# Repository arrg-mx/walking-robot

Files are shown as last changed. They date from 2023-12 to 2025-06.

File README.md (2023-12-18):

# ARRG: Curso ROS2 Humble, 2024-I - Walking Robot

## Contenido

- [Desarrollo](#desarrollo)
- [Equipo](#equipo)
- [Referencias](#referencias)

## Desarrollo

- [X ] Documentación y justificación de la configuración del robot.
- [X ] Planteamiento del modelo cinemático directo de la postura y planteamiento del modelo cinemático inverso de la postura.
- [ ] Diseño e implementación de un modelo virtual del caminante.
	- [X ] Modelo de una pierna del robot.
	- [ ] Modelo del robot completo.
- [ ] Realización de las pruebas dentro del modelo virtual y reporte de resultados.
- [ X] Construcción de un modelo físico del robot.
	- [ X] Construcción de una pierna del robot.
	- [ ] Construcción de la estructura del robot.
- [ ] Implementación de los resultados en el prototipo físico.
	- [ ] Prototipo de una pierna.
	- [ ] Prototipo del robot completo
- [ ] Reporte de resultados finales.
- [ ] Conclusiones y Discusión

## Equipo

**Integrantes del proyecto:**

| Nombre | Observaciones |
| :---| :--- |
| Hernández Romero Naomi Estefanía | **responsable** |
| Vargas Gutiérrez Kevin | |
| Hernández Hernández Danae Montserrat | |
| Martínez Merino Luis Eduardo | |

## Referencias

### ¿Dónde empezar?

**Artículos**

1. **Control of a Hexapod Robot Considering Terrain Interaction** [Arxiv Cornell University - article](https://arxiv.org/abs/2112.10206)
	> M. Zangrandi, S. Arrigoni, and F. Braghin, Control of a Hexapod Robot Considering Terrain Interaction. 2021. 
	> 
	> doi: 10.48550/arXiv.2112.10206
1. *Real-Time Stabilisation for Hexapod Robots* **DOI:** <https://doi.org/10.1007/978-3-319-23778-7_48>
	> M. Hörger, N. Kottege, T. Bandyopadhyay, A. Elfes, and P. Moghadam, “Real-Time Stabilisation for Hexapod Robots,” in Experimental Robotics: 
	> The 14th International Symposium on Experimental Robotics, M. A. Hsieh, O. Khatib, and V. Kumar, Eds. Cham: Springer International Publishing, 2016, pp. 729–744. 
	> 
	> doi: 10.1007/978-3-319-23778-7_48. 
1. **Kinematic and Dynamic Modeling of the PhantomX AX Metal Hexapod Mark III Robot using Quaternions**	[IEEE article](https://ieeexplore.ieee.org/abstract/document/9624596)
	> A. J. P. A. Chávez and J. H. A. Alcántara, "Kinematic and Dynamic Modeling of the PhantomX AX Metal Hexapod 
	> Mark III Robot using Quaternions," 2021 International Conference on Control, Automation and Information Sciences (ICCAIS), Xi'an, China, 2021, pp. 595-601, 
	>
	> doi: 10.1109/ICCAIS52680.2021.9624596.
1. **Dynamic Modeling and Control of the Hexapod Robot Using Matlab SimMechanics** [ResearchGate article](https://www.researchgate.net/publication/330405549_Dynamic_Modeling_and_Control_of_the_Hexapod_Robot_Using_Matlab_SimMechanics)
	> Beaber, Sameh & Zaghloul, Abdelrahman & Kamel, Mohamed & Hussein, Wessam. (2018). Dynamic Modeling and Control of the Hexapod Robot Using Matlab SimMechanics. 
	> V04AT06A036. 10.1115/IMECE2018-88226. 
	>
	> DOI:10.1115/IMECE2018-88226
1. **Locomotion Control of PhantomX Hexapod Robot with Touch-Pressure Sensor and RoboComp**	[ResearchGate article](https://ieeexplore.ieee.org/abstract/document/9247874).
	> J. E. C. Fuertes, J. J. M. Arciniegas, P. B. G. de Castro and O. A. V. Albán, "Locomotion Control of PhantomX Hexapod Robot with Touch-Pressure Sensor and RoboComp," 
	> 2020 IEEE Colombian Conference on Applications of Computational Intelligence (IEEE ColCACI 2020), Cali, Colombia, 2020, pp. 1-6, 
	> 
	> doi: 10.1109/ColCACI50549.2020.9247874.
1. **Dynamic modeling and real-time evaluation of reaction forces and torques of hexapod robot** [ResearchGate article](https://www.researchgate.net/publication/350820943_Dynamic_modeling_and_real-time_evaluation_of_reaction_forces_and_torques_of_hexapod_robot)
	> S. Beaber, A. Zaghloul, M. Kamel, and W. Hussein, “Dynamic modeling and real-time evaluation of reaction forces and torques of hexapod robot,” Apr. 2021, p. 30. 
	> 
	> doi: 10.1117/12.2596113. 
1. **Design, Construction, and Rough-Terrain Locomotion Control of Novel Hexapod Walking Robot With Four Degrees of Freedom Per Leg** [IEEE article](https://ieeexplore.ieee.org/abstract/document/9330519)
	> P. Čížek, M. Zoula and J. Faigl, "Design, Construction, and Rough-Terrain Locomotion Control of Novel Hexapod Walking Robot With Four Degrees of Freedom Per Leg," 
	> in IEEE Access, vol. 9, pp. 17866-17881, 2021, 
	>
	> doi: 10.1109/ACCESS.2021.3053492.

**Blogs**

1. *Love, Death, and Robot simulators* [medium post](https://medium.datadriveninvestor.com/love-death-and-robot-simulators-9ad7c62d46ae). 
	- **Posted by:** [Mithi](https://medium.com/@mithi?source=post_page-----9ad7c62d46ae--------------------------------)
	- **Published:** March 30, 2020
	- **Posted in:** [DataDrivenInvestor](https://medium.datadriveninvestor.com/?source=post_page-----9ad7c62d46ae--------------------------------)
	- **Source Code:**
 		- **Mithi's Bare-Minimum Hexapod Robot Simulator 2** [Github repository](https://github.com/mithi/hexapod)
		- **Hexapod Kinematics Library** [Github repository](https://github.com/mithi/hexapod-kinematics-library). By [**Mithi Sevilla´s** Github Profile](https://github.com/mithi). Code you can use to solve forward/inverse kinematics and generate walk sequences of hexapod robots. 
 	- **Live demo:** <https://hexapod.netlify.app/>
  	- **Hexapod Robot Inverse kinematics Visualizer (with Javascript and React)** [YT video](https://www.youtube.com/watch?v=FxjfTUj2Dk0)
	- **Tags:** [Robotics](https://medium.com/tag/robotics?source=post_page-----9ad7c62d46ae---------------robotics-----------------), 
	[Artificial Intelligence](https://medium.com/tag/artificial-intelligence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), 
	[Open Source](https://medium.com/tag/open-source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), 
	[Electronics](https://medium.com/tag/electronics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), 
	[Coding](https://medium.com/tag/coding?source=post_page-----9ad7c62d46ae---------------coding-----------------)

**Legacy/Opensource Projects, Applications and, Libraries**

1. **Interbotics ROS Crawlers** [github repository](https://github.com/Interbotix/interbotix_ros_crawlers). ***ROS2 Humble*** *Compatible*
	- This repo contains custom ROS packages to control the various types of crawlers sold at [Interbotix](https://www.trossenrobotics.com/). 
	- These ROS packages build upon the ROS driver nodes found in the [interbotix_ros_core](https://github.com/Interbotix/interbotix_ros_core) *repository*. 
	- Support-level software can be found in the [interbotix_ros_toolboxes](https://github.com/Interbotix/interbotix_ros_toolboxes) *repository*.
1. **PhantomX Hexapod Mark II**
	- Google search [results](https://www.google.com/search?client=firefox-b-d&q=PhantomX+Hexapod+Mark+II)
	- **PhantomX AX Metal Hexapod MK-III Kit** [Trossen Robotics #Item](https://www.trossenrobotics.com/phantomx-ax-hexapod.aspx)
	- **PhantomX AX Metal Hexapod Mark III** [YT video](https://www.youtube.com/watch?v=8v16kpBj9JQ). [Trossen Robotics - YT channel](https://www.youtube.com/@InterbotixTrossenRobotics)
	- **PhantomX Hexapod Mark II** [GrabCad model](https://grabcad.com/library/phantomx-hexapod-mark-ii-1)
	- **HumaRobotics**
		- **phantomx_description** [github repository](https://github.com/HumaRobotics/phantomx_description)
		- **phantomx_control** [github repository](https://github.com/HumaRobotics/phantomx_control)
		- **phantomx_gazebo** [github repository](https://github.com/HumaRobotics/phantomx_gazebo)
		- **geomagic_touch** [github repository](https://github.com/HumaRobotics/geomagic_touch)
	- **PhantomX Hexapod Examples Various demos for the PhantomX Hexapod** [github repository](https://github.com/Interbotix/PhantomXHexapodExamples)
1. **hexapod-robot** [github repository](https://github.com/ibarbech/hexapod-robot)
1. **ROS Hexapod Stack** [github repository](https://github.com/KevinOchs/hexapod_ros/tree/master)
1. **Syropod High-level Controller** [Github repository](https://github.com/csiro-robotics/syropod_highlevel_controller)
	- **OpenSHC: A Versatile Multilegged Robot Controller** [YT video](https://www.youtube.com/watch?v=-E7-2UMP5XU)
	- **Note:** The codebase is largely copied from [Mithi's Bare Minimum Hexapod Robot Simulator 2](https://github.com/mithi/hexapod).
1. **Hexi** *(project)* [about](https://hexyrobot.wordpress.com/)
	- [Github repository](https://github.com/mithi/hexy)
1. **TOPS** *(Traverser of Planar Surfaces) or SPOT backward is a 12DOF quadrupedal robot.*
	- [project page](https://www.aaedmusa.com/projects/tops)
 	- [Hackaday's project page](https://hackaday.io/project/192122-tops)
  	- CAD, Code, BOM, etc... [Github repository](https://github.com/aaedmusa/TOPS)
   	- *I Built a Robotic Actuator.......Lets Test it!* [Part 0 - YT video](https://www.youtube.com/watch?v=gxXatMr0LX4)
   	- *Robot Dog Part 1: Leg Day* [Part 1 - YT video](https://www.youtube.com/watch?v=cqpYpj8EaDY)
   	- *Robot Dog Part 2: Leg Redesign* [Part 2 - YT video](https://www.youtube.com/watch?v=bdJuIe2igCI)
   	- *I Built a Robot Dog and Made it Dance* [Part 3 - YT video](https://www.youtube.com/watch?v=VhUvoV5XyRg)
1. **openDog V3: How I made it Walk** [YT video](https://www.youtube.com/watch?v=eKZIJwJBjEs). By [James Bruton](https://www.youtube.com/@jamesbruton)
	- *CAD and code* [openDogV3- Github repository](https://github.com/XRobots/openDogV3) 

---

**Nota:** Usar la siguiente [plantilla](https://github.com/arrg-mx/fmtos-docs/blob/main/fmto-reporte-curso.md) para su reporte así como la [plantilla del repositorio](https://github.com/mrg-mex/mrg-plantilla-repositorio) como una guía para organizar sus archivos y referencia del formato Markdown para diferentes elementos que necesiten integrar en su reporte.

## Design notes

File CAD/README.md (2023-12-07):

# Carpeta para archivos de CAD del proyecto
Los archivos de todo el CAD se encuentran en el archivo comprimido Modelos.rar

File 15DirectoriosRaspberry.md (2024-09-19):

# Creacion del entorno de trabajo 

> mkdir ROS2_dev

>cd ROS2_dev

>mkdir hexapod_ws

>cd hexapod_ws

>mkdir src

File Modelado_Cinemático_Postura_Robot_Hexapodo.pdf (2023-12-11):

## UNIVERSIDAD NACIONAL AUTÓNOMA DE MÉXICO

## Facultad de Ingeniería Ingeniería Mecatrónica

# ROBÓTICA

## Proyecto Final - Robot Hexapodo

## Profesor: Erik Peña Medina

## Integrantes: - Capulín Ornelas Arturo Misael - Hernández Hernández Danae Monserrat - Hernández Romero Naomi Estefanía - Jiménez Díaz César David - Vargas Gutiérrez Kevin

## Ciudad de México, 08 de diciembre de 2023

## Modelado de la pata del hexapodo en el espacio

## Método de transformaciones homógeneas

El método de transformaciones homógeneas consiste en describir las relaciones de posición y orientación entre cada uno de los elementos que conforman la estructura mecánica de un robot, para describir dichas relaciones se establece una matriz la cual contiene las relaciones entre las translaciones sobre cada uno de los ejes y las rotaciones sobre cada uno de los ejes. En la Figura (3), se presentan las relaciones que describen las
translaciones para describir a posición del orienten de un sistema | con respecto el origende un sistema
anterior | .

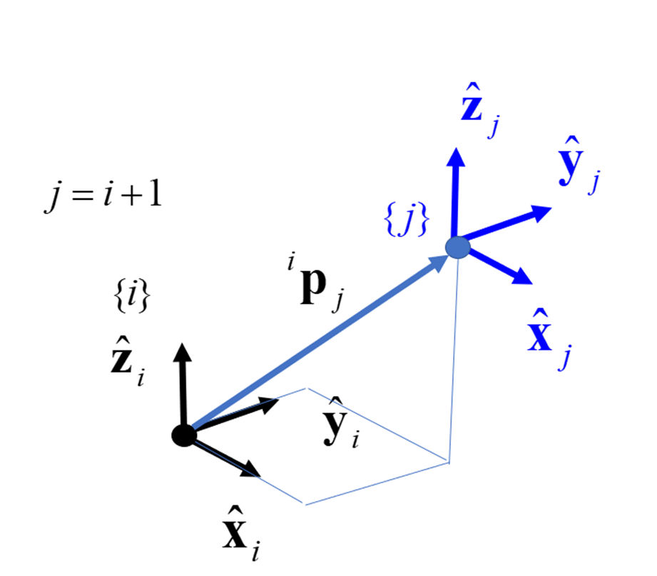
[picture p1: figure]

Figura 3. Planteamiento de la descripción de la posción del sistema | con respecto a un sistema | .
La posición del sistema | con respecto al sistema | , se compone de tres transformaciones que describen
las translaciones sobre cada uno de los ejes coordenadas del sistema | .

Las posición del sistema | con respecto al sistema | se describe mediante la combinación de las
transformaciones anteriores, conformando la transformación | :

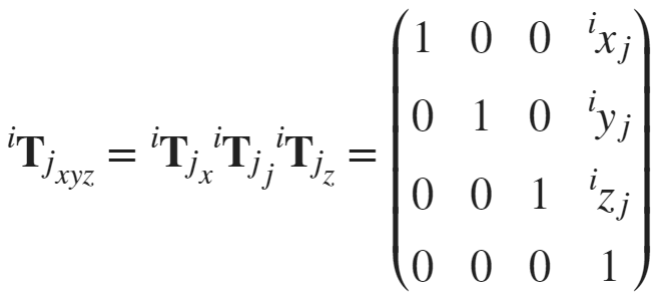
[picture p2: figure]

La orientación del sistema de referencia se establece mediante la combinación de matrices que contiene las relaciones de orientación con respecto a cada uno de los ejes del sistema .

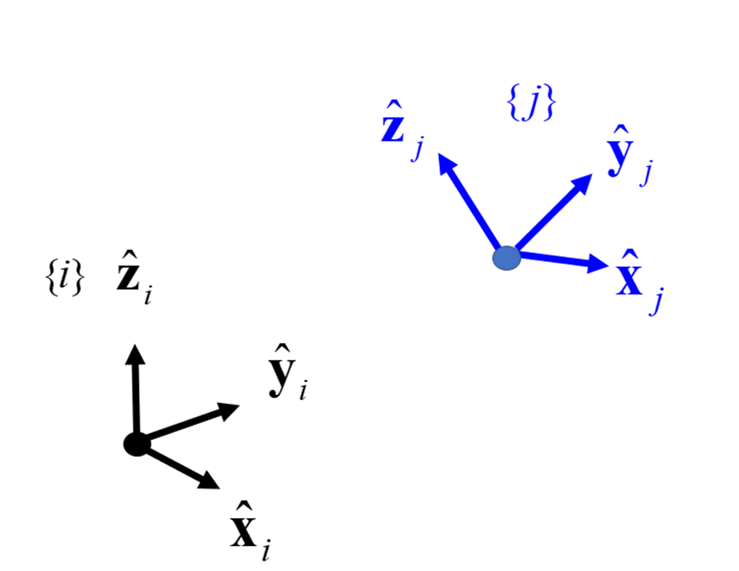
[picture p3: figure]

Figura 4. Planteamiento de la descripción de la orientación del sistema | con respecto a un sistema | .
Las relaciones que describen la orientación al eje | (Figura 5) se establece mediante la transformación

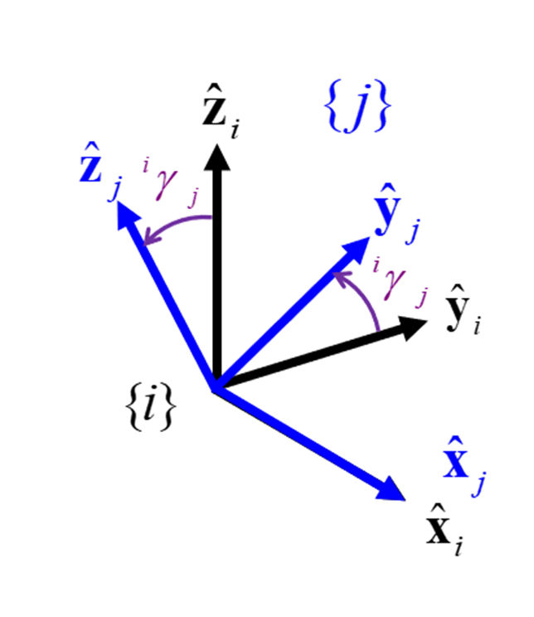
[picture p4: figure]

Figura 5. Planteamiento de la descripción de la orientación del sistema | con respecto a un sistema | con
respecto al eje .

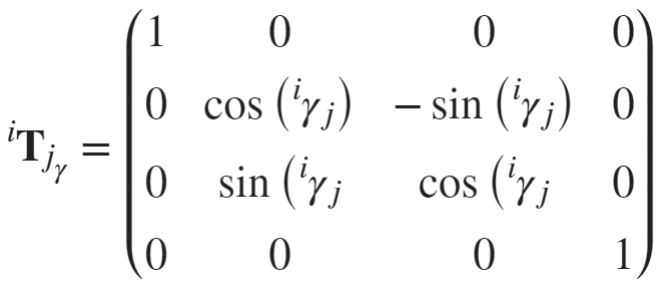
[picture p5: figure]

Las relaciones que describen la orientación al eje | (Figura 6) se establece mediante la transformación | .

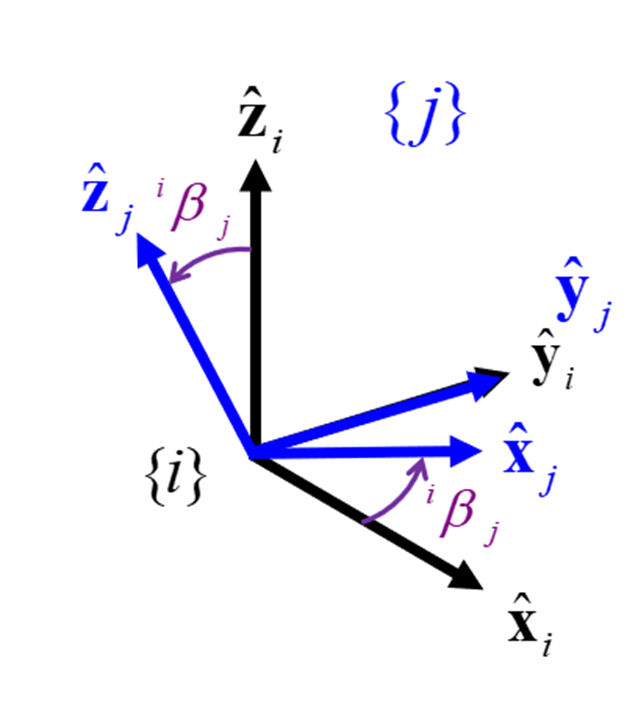
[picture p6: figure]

Figura 6. Planteamiento de la descripción de la orientación del sistema | con respecto a un sistema | con
respecto al eje .

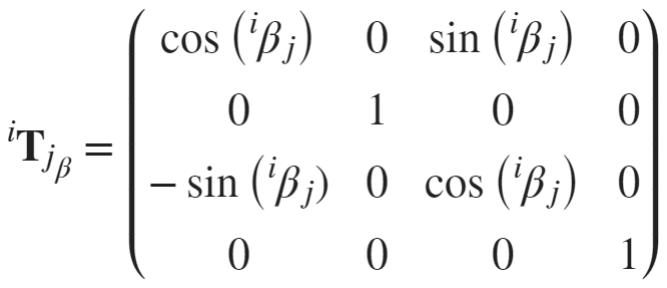
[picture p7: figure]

Las relaciones que describen la orientación al eje | (Figura 7) se establece mediante la transformación | .

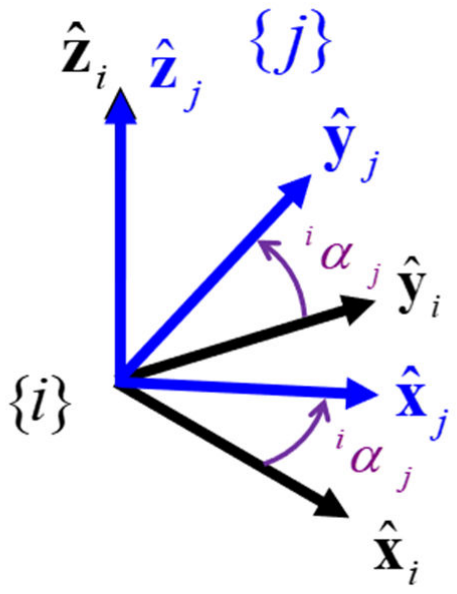
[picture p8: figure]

Figura 7. Planteamiento de la descripción de la orientación del sistema | con respecto a un sistema | con
respecto al eje .

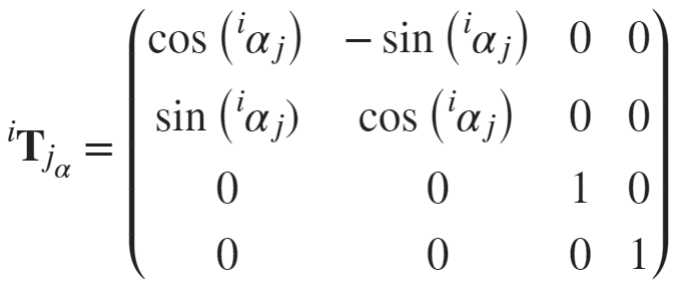
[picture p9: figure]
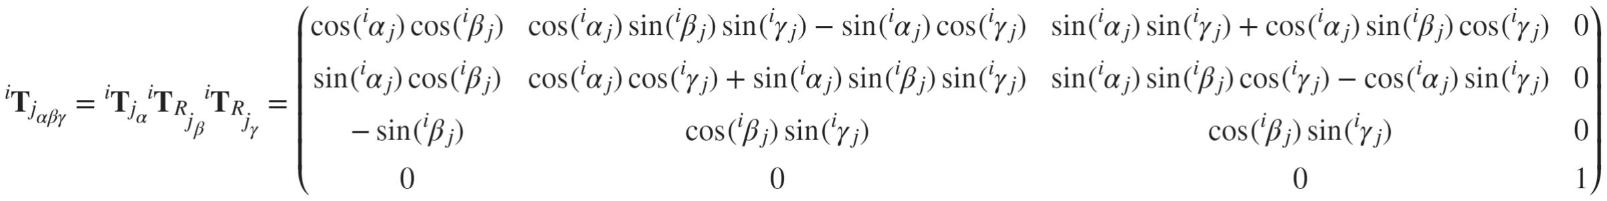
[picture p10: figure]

Para conformar la transformación que describre las relaciones de posición y orientación entre dos sistemas de referencias se establece la transformación :

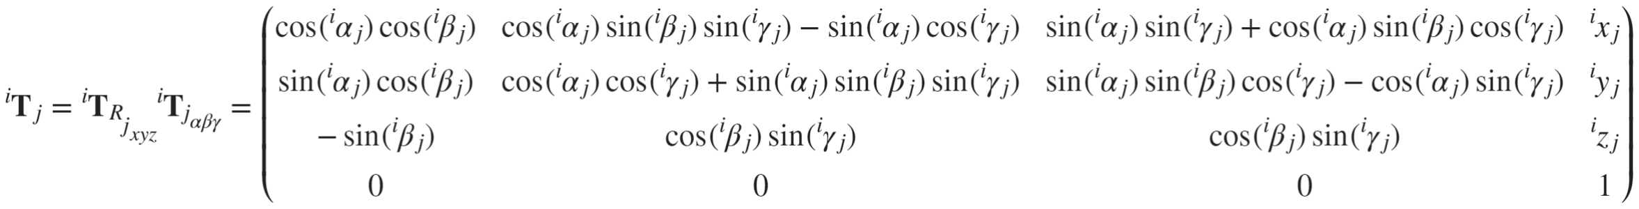
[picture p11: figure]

Para mostrar como se emplean las transformaciones homógeneas se plantea el ejemplo en el cual se obtiene el modelo matemático de la postura de un robot PUMA 560.

Planteamiento del modelo de la postura por el método de transformaciones homógenas

Para establecer el modelo cinemático de la postura de la pata del hexapodo es necesario definir una postura de "Home" en la cual el robot comezará a operar de forma segura, además de la cual se establecerán las ecuaciones que describan al robot. Ya definida la postura de "Home", se debe de seguir los siguientes pasos para establecer el modelo matemático que describa la postura de un robot en función de sus variables de postura:

1. Determinar el sistema inercial.
2. Encontrar los ejes de acción de los actuadores.
3. Sobre los ejes de actuación establecer los sistema de referencias que rescriban las relaciones de movimiento entre una junta y un eslabón.
4. Establecer los parámetros y las variables de posición y orientación entre los sistemas de referencia de cada eslabón hasta llegar el sistema {P}.
5. Colocar los parámetros en la tabla de configuración y de variables.
6. Calcular la ecuación del modelo cinemático de la postura.

1.Determinación del sistema inercial

Para establecer un sistema el modelo un robot es necesario establecer un sistema de referencia por el cual se estableceran las relaciones posición y orientación del efector final de un robot, para este caso se establecerá
un sistema inercial el cual permanecerá fijo y se establecerá como el sistema | y un sistema de referencia
relativo | asociado al EF del robot.

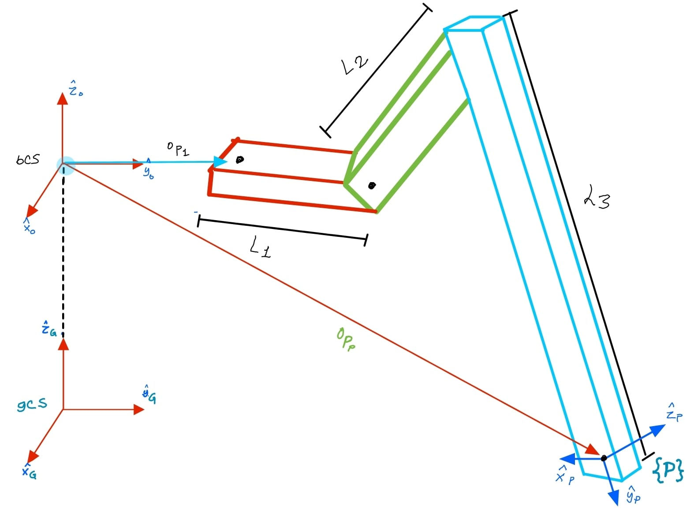
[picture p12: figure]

Figura 1. Planteamiento del sistema inerical | y del sistema de referencia | asociado al EF del robot.

### 2. Encontrar los ejes de acción de los actuadores

Dentro del diagrama del robot se identifican los ejes de actuación asociados con cada una de las juntas del robot, para este caso el robot tiene 3 grados de libertad (GDL), por lo que en el diagrama del robot se identificaran 3 ejes de acción de los actuadores (Figura 2)

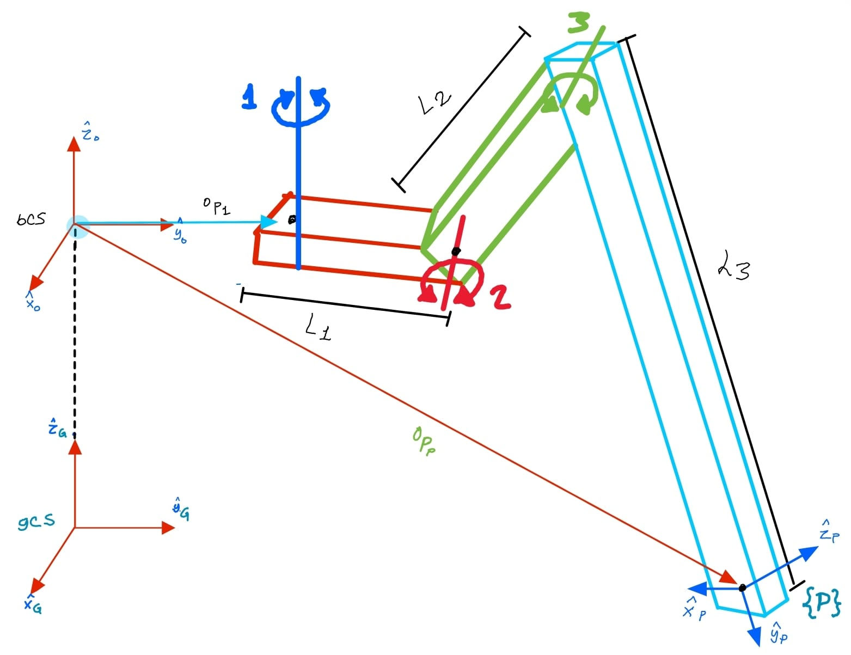
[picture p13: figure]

Figura 2. Ejes de actuación relacionadas de las juntas del robot.

### 3. Establecimiento de los sistemas de refencia

Para describir las relaciones de movimeinto y de orientación entre cada uno de los eslabones se establecen sistemas de refencia asociados a cada una de las juntas y cada eslabón. Para definir los sistemas de referencia en este método de cada una de las juntas se deben seguir las siguientes consideraciones:

- Se establecerá un sistema de referencia por junta y eslabón, y serán numerados en orden asendente, para este planteamiento a cada junta se le asociará un número y en el caso del EF del robot su sistema de referencia se definira como {P}.
- Sobre los ejes relacionados con las juntas de actuación es necesario definir un punto el cual será el origen cada uno de los sistemas de referencia, por lo que es necesario que cada uno de estos puntos tengan una relación interna con la estructura del robot.

- Definidos el origen de cada uno de los sistemas de referencia se establecen los ejes que los conforman de tal manera que uno de estos concida con el eje de actuación, la disposición los ejes debe permitir que los parámetros que describen las posición de los sistemas de referencia deben ser positivas, aunque cabe resaltar que hay casos donde cuando menos algún parámetros tendra un valor negativo.
- En el caso de las juntas sean rotacionales, su actuación se indicara mediante un ángulo .

En la Figura 3, se presenta el planteamiento de los sistemas de referencia establecidos para describir las relaciones de posición y orientación de cada uno de los eslabones que componen la pata del robot.

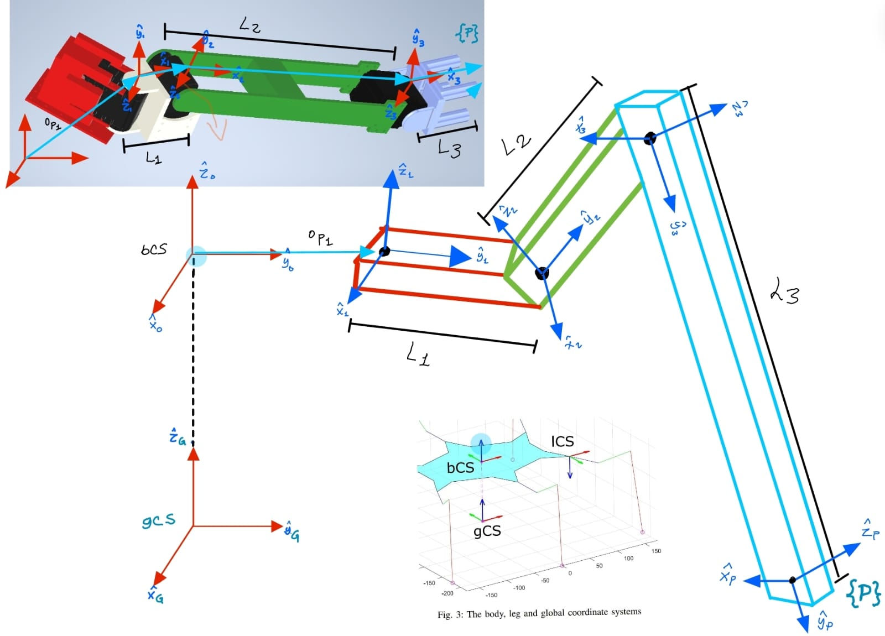
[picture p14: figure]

Figura 3. Planteamiento de los sistemas de referencia para pata del hexapodo.

### 4. Planteamiento de los parámetros

El planteamiento de los parámetros y de las variables se establecen entre cada uno de los sistemas de
referencia, en la Figura 4, se presentan las relaciones de posición y orientación entre el sistema | y el
sistema | , donde el ángulo | es la rotación del sistema | con respecto al eje | y se mide entre la

dirección el eje | y la dirección del eje | y el vector de posición | se compone por una

componente de translación en la dirección positiva del en la dirección del eje .

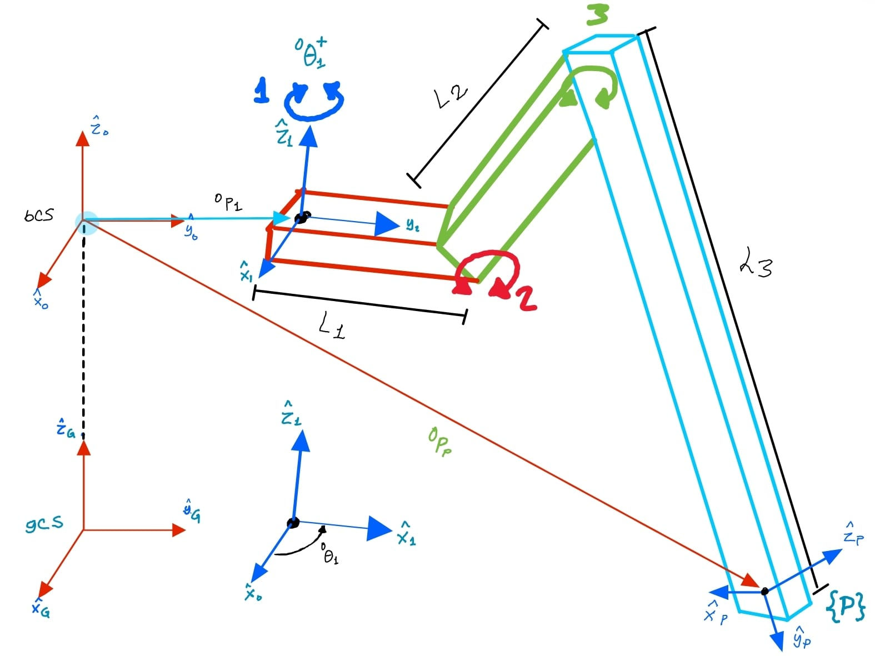
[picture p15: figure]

Figura 4. relaciones de posción y orientación entre el sistema | con respecto al sistema | .
En la Figura 5, se presentan las relaciones de posición y orientación entre el sistema | con respecto al
sistema | , donde el cual el sistema el sistema | gira con respecto al eje | un ángulo | el cual se mide
entre la dirección del eje | y la dirección del eje , y el vector de posición | se compone por
una componente de translación en la dirección positiva del en la dirección del eje .

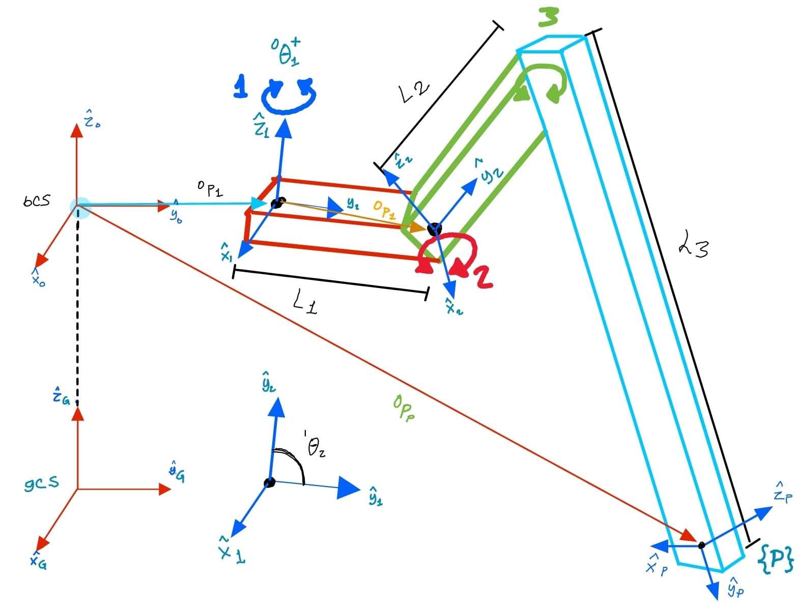
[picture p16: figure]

Figura 5. relaciones de posción y orientación entre el sistema | con respecto al sistema | .
En la Figura 6, se presentan las relaciones de posición y orientación entre el sistema | con respecto al
sistema | , donde el cual el sistema el sistema | gira con respecto al eje | un ángulo | el cual se mide
entre la dirección del eje | y la dirección del eje , y el vector de posición | se compone por
una componente de translación en la dirección positiva en la dirección del eje .

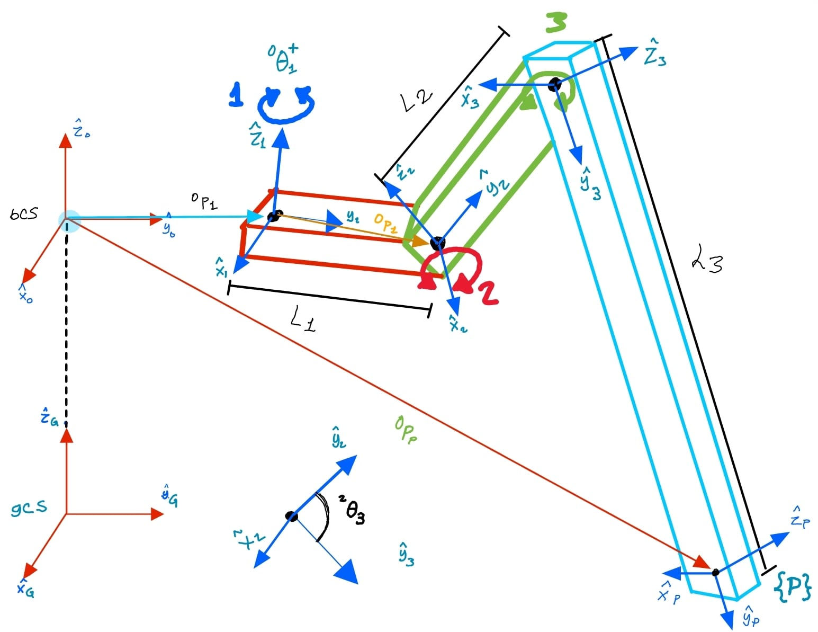
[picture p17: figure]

Figura 6. relaciones de posción y orientación entre el sistema | con respecto al sistema | .

### 5. Tabla de parámetros y variables

La información que describe la relación entre los parámetros de posición y orientación de los eslabones se vacia en la siguiente tabla con el fin de establecer las transformaciones que describen las relaciones entre los sistemas de referencia.

Tabla 1. Parámetros de la configuración y la postura del robot.

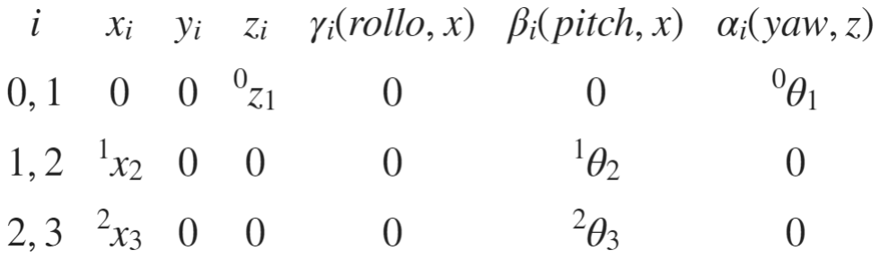
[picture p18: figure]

### 6. Calculo del modelo cinemático de la postura

Los elementos que conforman a un reglon conforman una tabla

Tij(x_i_j, y_i_j, z_i_j, gi_j, bi_j, ai_j) =

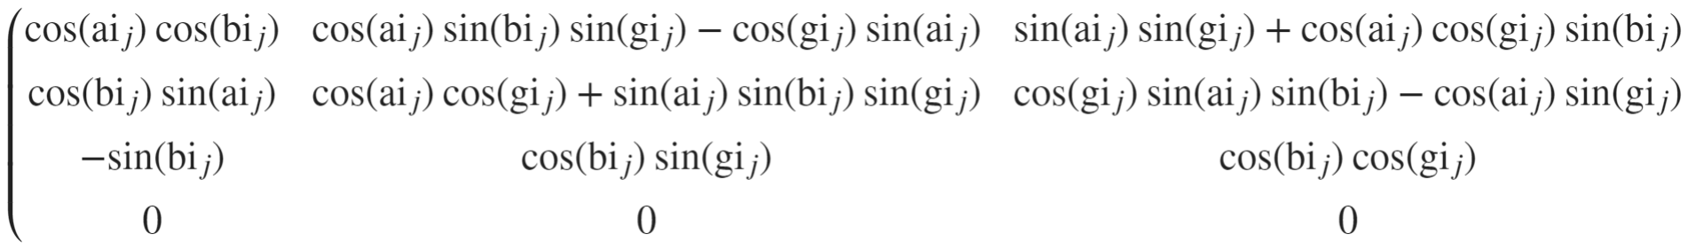
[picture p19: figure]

Cálculo de las tranformaciones, cálculo de la tranformación general:

Traslación del sistema BCS al Sistema de coordenadas [1]

TT0_1 =

Transformada de

Rotación en el eje

TR1_2 =

Traslación en el eje

TT1_2 =

T1_2 =

Transformada de

T1_2 =

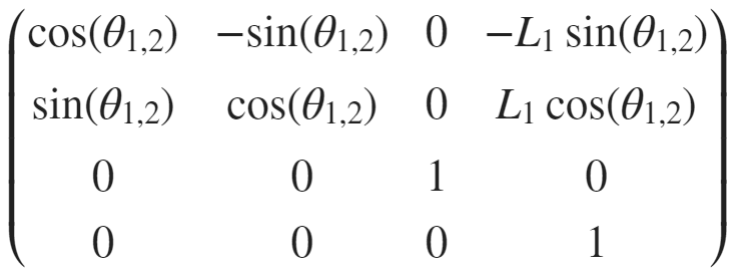
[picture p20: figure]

Rotación en el eje

TR2_3 =

Traslación en el eje

TT2_3 =

Transformada de

T2_3 =

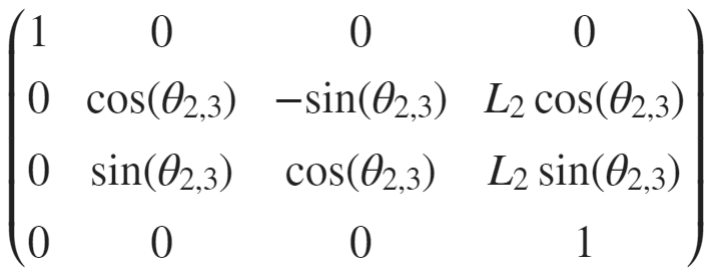
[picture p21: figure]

Rotación en el eje

TR3_p =

Traslación en el eje

TT3_P =

Transformada de

T3_p =

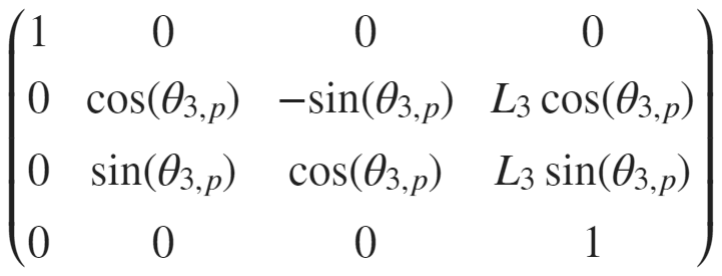
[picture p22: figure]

Transformada de

T0_P =

T0_p =

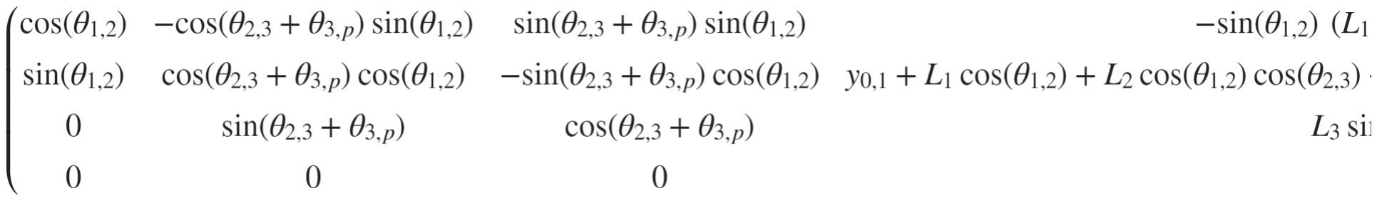
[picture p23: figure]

Extremo de la pata, Efector final (P)

P = 4×1
0
0
0
1
La Cinematica directa de la postura de la pata, es igual a:

Post =

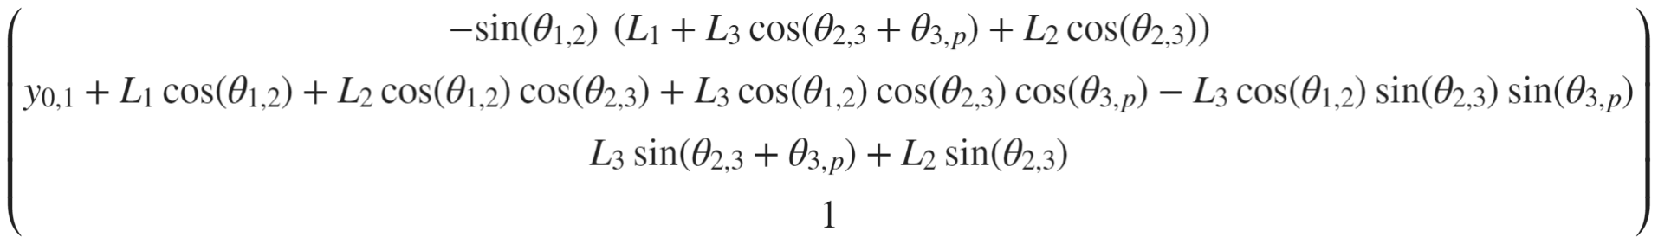
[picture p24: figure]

Resultados
El objetivo de este proyecto fue el desarrollo de un robot hexápodo. El robot cuenta con seis patas, cada una con tres articulaciones. El modelo cinemático de la postura del robot se planteó a partir de las relaciones entre las articulaciones y los puntos de referencia del robot.

El robot hexapodo presentado en el trabajo se logró realizar de manera satisfactoria obteniendo los resultados de las matrices empleadas para su diseño. Con ayuda del método para el plantemiento del modelo cinemático de la postura trazamos los distintos ejes de referencia para modelar los movimientos y ángulos que tomaría el movimiento de una pata.

Las matrices empleadas para un modelo cinemático de postura aplicado a un robot hexápodo son las matrices de transformación homogénea. Estas matrices permiten representar la transformación de un punto del espacio a otro, a través de una combinación de traslación, rotación y escalado.

En el caso de un robot hexápodo, las matrices de transformación homogénea se utilizan para representar la transformación de la base del robot a la punta de cada pata. Para ello, se necesita conocer la posición y orientación de la base del robot, así como la posición y orientación de cada articulación de la pata.

Para obtener la matriz de transformación homogénea para la punta de una pata, se pueden multiplicar las matrices de transformación homogénea de cada articulación de la pata.

En los esquemas mostrados anteriormente, se puede ver que la matriz de transformación homogénea para la punta de la pata se puede obtener a partir de la multiplicación de las matrices de transformación homogénea de las articulaciones 1, 2 y 3.

La matriz final de la cinemática directa de la postura es la matriz de transformación homogénea para la punta de la última pata del robot.

La matriz final de la cinemática directa de la postura nos permite determinar la posición y orientación de la base del robot a partir de las posiciones y orientaciones de las articulaciones. Esta matriz se obtuvo a partir de la aplicación de la ley de los cosenos y la ley de los senos.

El éxito del proyecto se debe a que el modelo cinemático de la postura se planteó de manera acertada, lo que permitió obtener una matriz final exacta. El resultado final es que el robot puede moverse de manera controlada y precisa, lo cual es posible gracias a la información proporcionada por la matriz final.

A continuación, se detallan los aspectos más relevantes:

- Lo que nos dice la matriz final de la cinemática directa de la postura:

La matriz final de la cinemática directa de la postura nos permite determinar la posición y orientación de la base del robot a partir de las posiciones y orientaciones de las articulaciones. Esta información es necesaria para el control del robot, ya que permite determinar la ubicación y dirección del robot en el espacio.

- Por qué obtuvimos estos resultados:

Se obtuvieron debido a que el modelo cinemático de la postura se planteó de manera correcta. El modelo cinemático es la base para el control del robot, por lo que es importante que esté bien planteado.

- Cuál es el resultado final:

El resultado final es que el robot puede moverse de manera controlada y precisa. Esto se debe a que la matriz final de la cinemática directa de la postura permite determinar la posición y orientación de la base del robot a partir de las posiciones y orientaciones de las articulaciones.
Referencias:
[1] M. A. C. Verdugo, Diseño, Construcción y control de un robot hexápodo, Ciudad universitaria, México D.F.: UNAM, 2011.

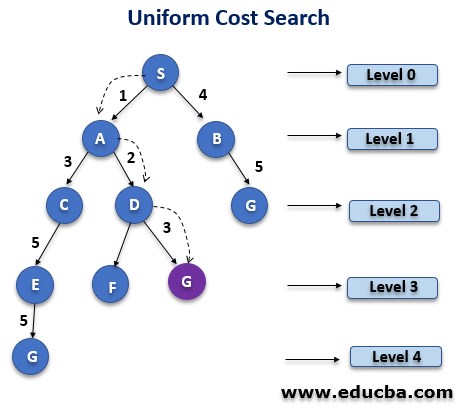
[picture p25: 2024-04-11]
Bitácora/Imágenes/Uninformed-Search-4.jpg

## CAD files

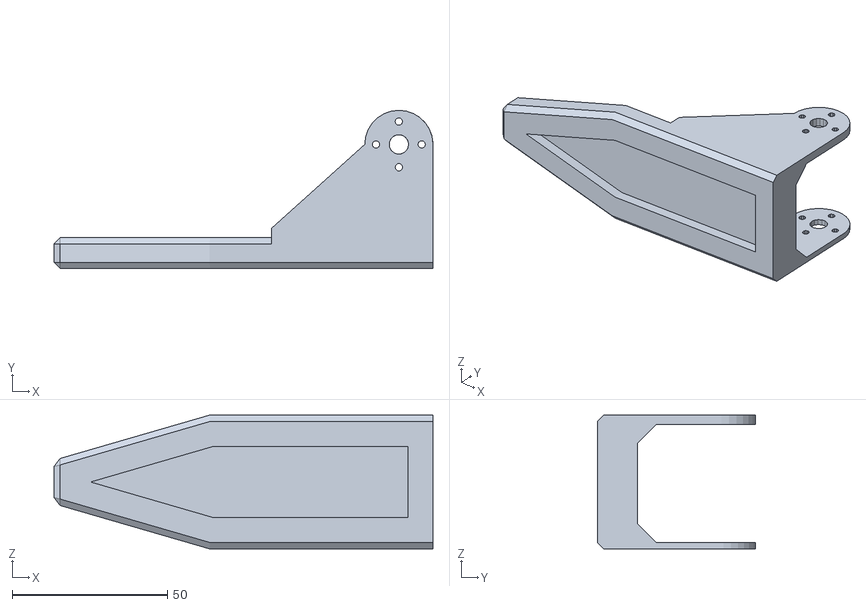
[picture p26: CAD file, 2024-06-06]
CAD_NAOMIV2/HEXAPODV2CAD/tibia.stl
122.0 x 51.0 x 43.0

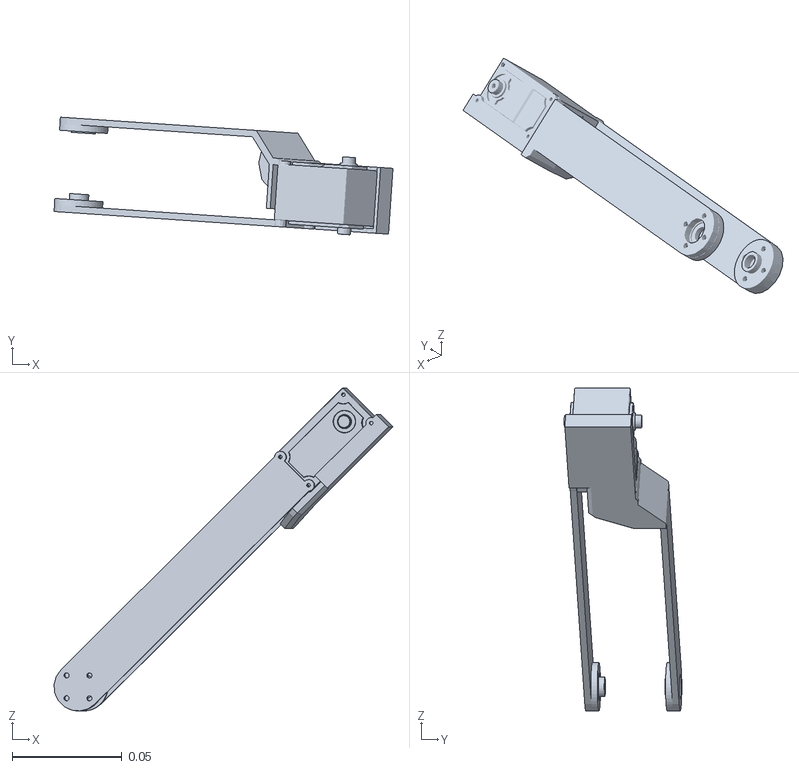
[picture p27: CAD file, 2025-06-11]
hexapod_description/meshes/4B_link.STL
0.154 x 0.0535 x 0.147

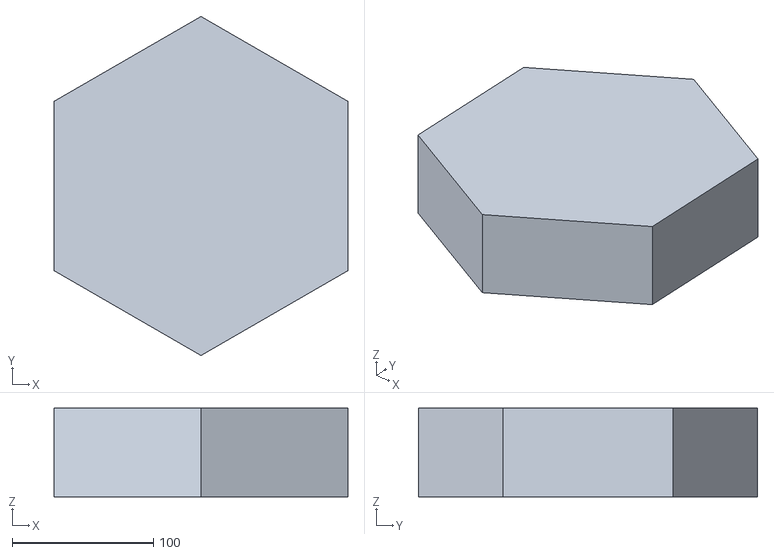
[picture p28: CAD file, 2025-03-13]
Modelos Simulacion/HEXAGONO_.stl
207.8 x 240.0 x 63.0

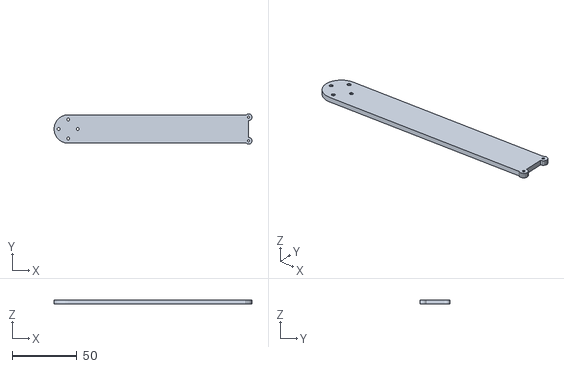
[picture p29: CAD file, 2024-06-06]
CAD_NAOMIV2/HEXAPODV2CAD/tibiaMot.stl
152.7 x 23.4 x 3.00

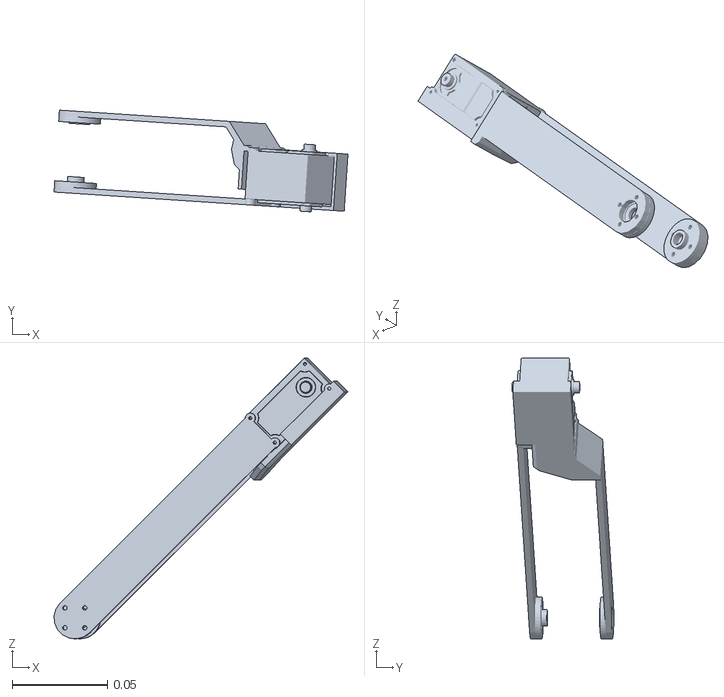
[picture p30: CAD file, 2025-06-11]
hexapod_description/meshes/5B_link.STL
0.154 x 0.0533 x 0.147

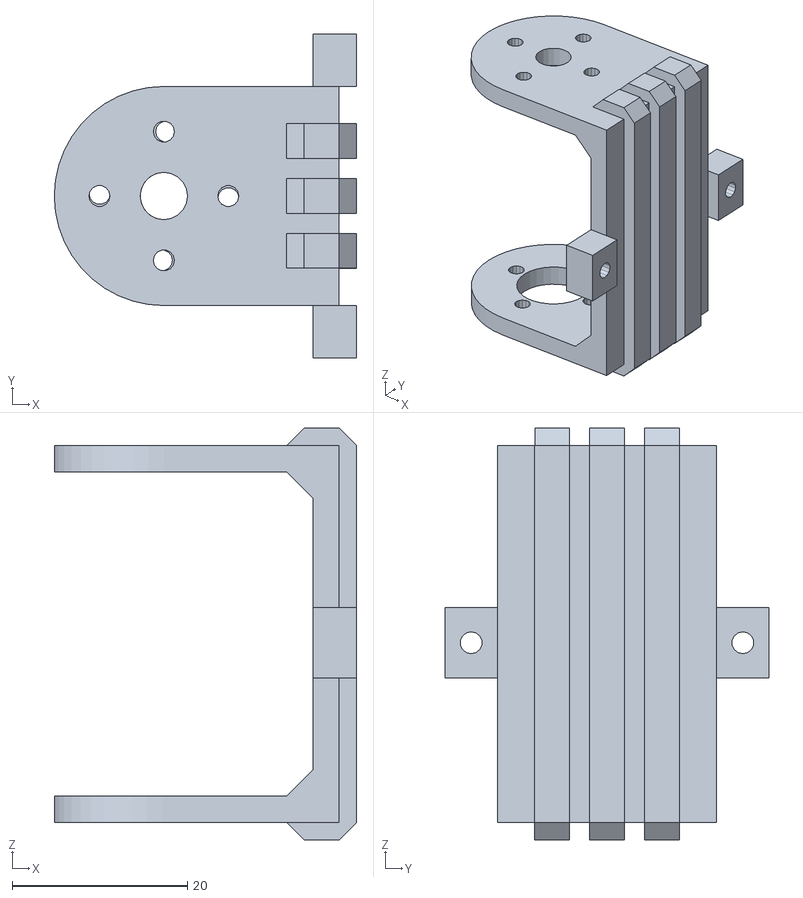
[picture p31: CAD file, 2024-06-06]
CAD_NAOMIV2/HEXAPODV2CAD/UnionCuerpo.stl
34.5 x 37.0 x 47.0

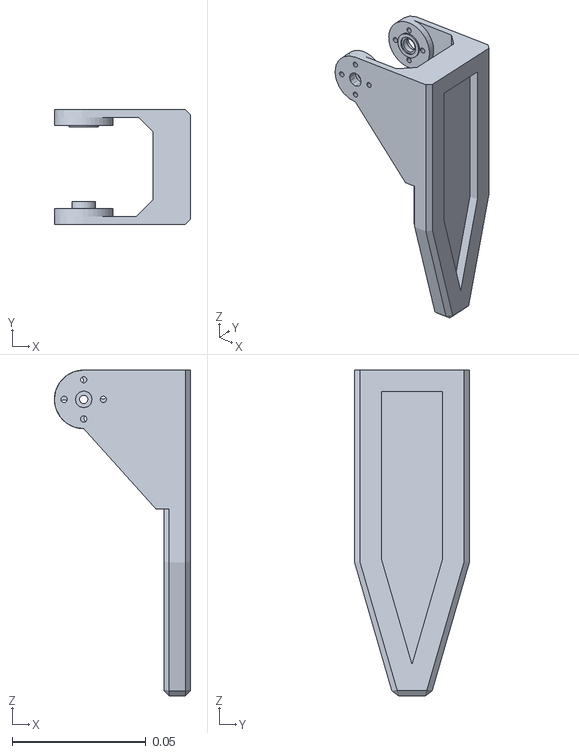
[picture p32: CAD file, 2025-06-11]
hexapod_description/meshes/2C_link.STL
0.051 x 0.043 x 0.122

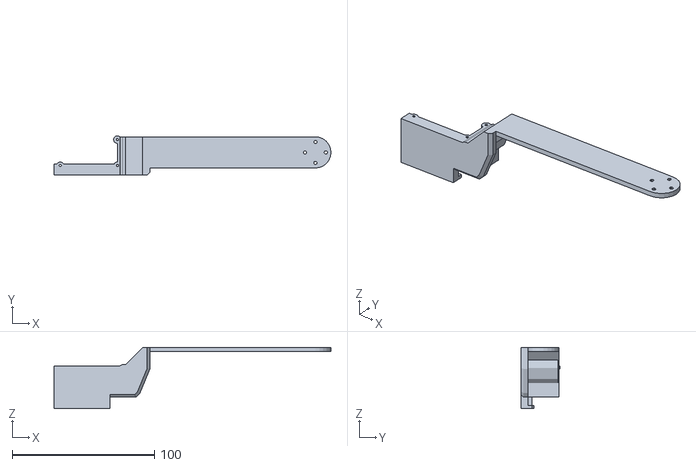
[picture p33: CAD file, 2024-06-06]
CAD_NAOMIV2/HEXAPODV2CAD/femurAux.stl
194.7 x 27.7 x 43.0

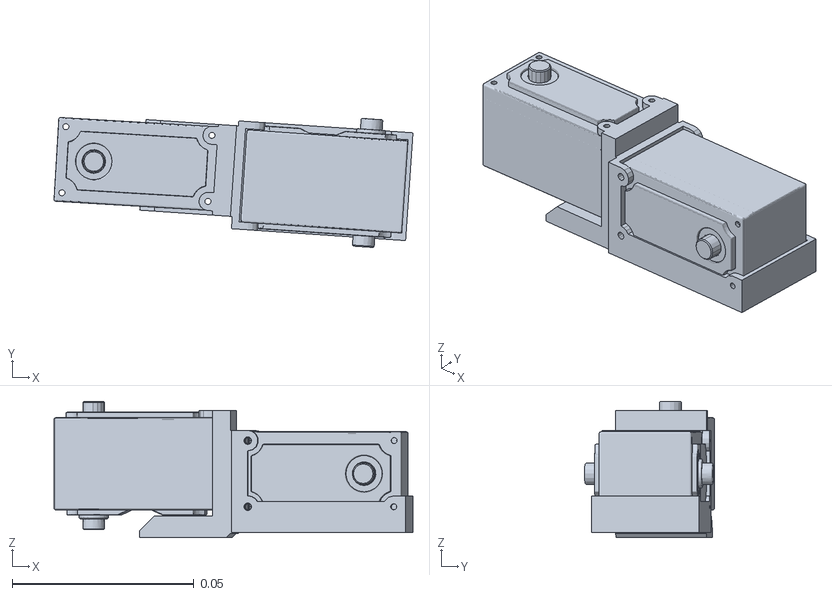
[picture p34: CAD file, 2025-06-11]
hexapod_description/meshes/6A_link.STL
0.0987 x 0.0357 x 0.0375

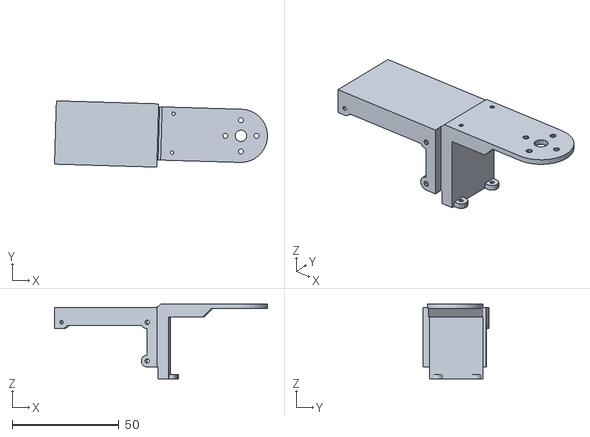
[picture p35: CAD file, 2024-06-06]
CAD_NAOMIV2/HEXAPODV2CAD/Coxa.stl
99.9 x 31.1 x 35.0

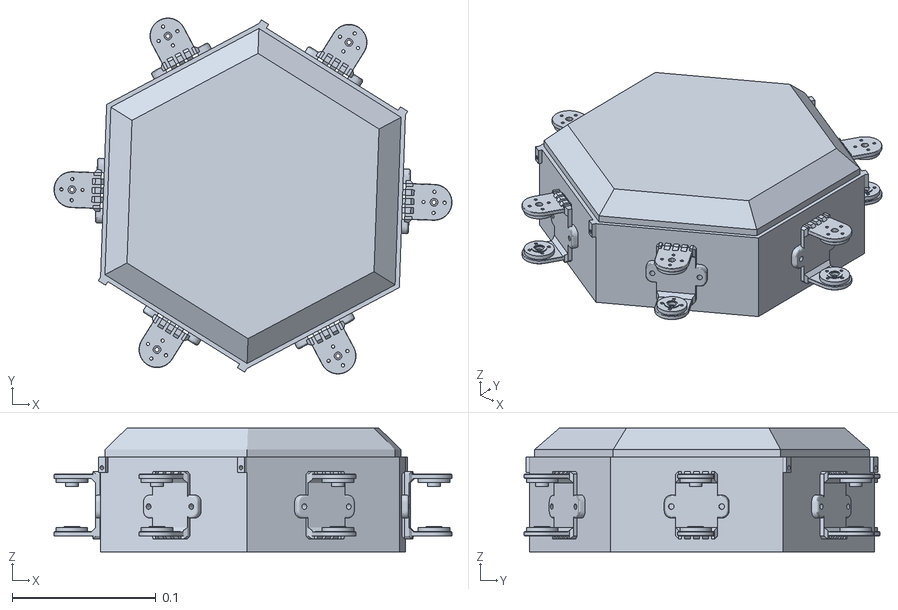
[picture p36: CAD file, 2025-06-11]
hexapod_description/meshes/base_link.STL
0.277 x 0.247 x 0.086

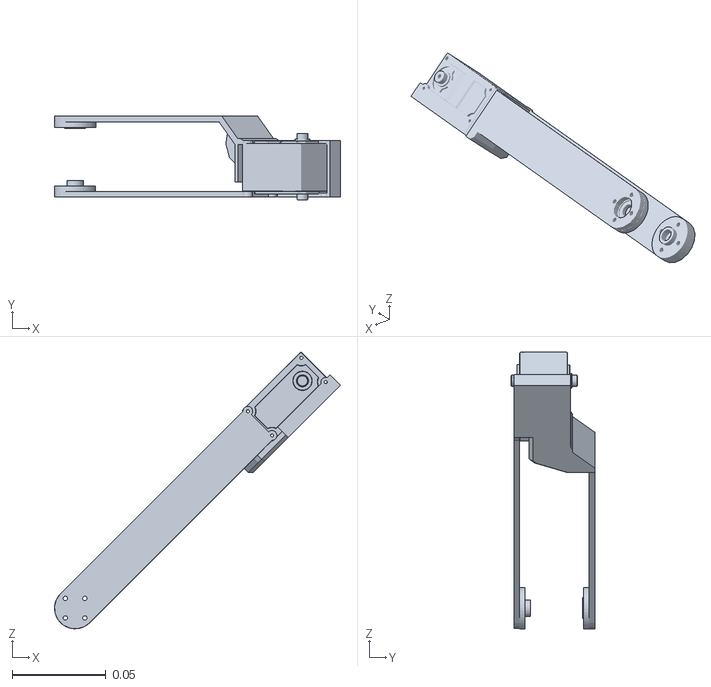
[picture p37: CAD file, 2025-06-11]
hexapod_description/meshes/2B_link.STL
0.152 x 0.0445 x 0.147

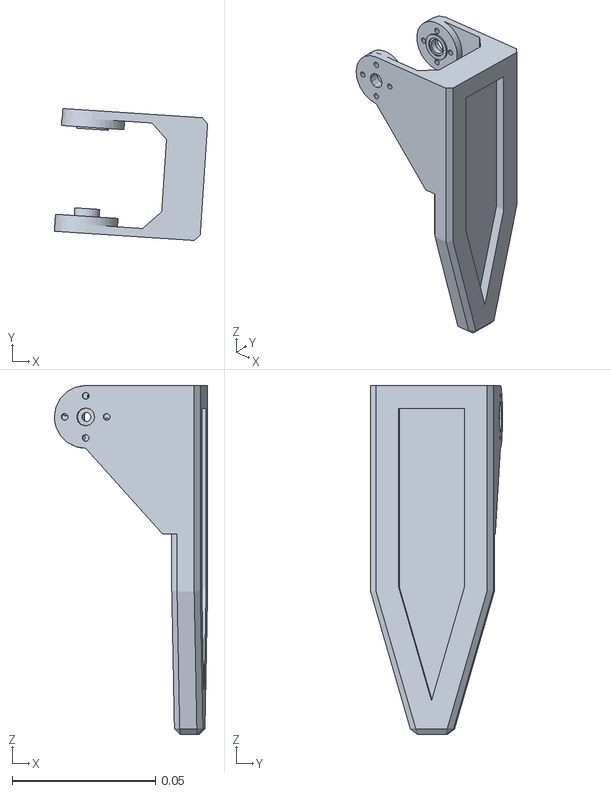
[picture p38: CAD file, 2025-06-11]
hexapod_description/meshes/5C_link.STL
0.0536 x 0.0461 x 0.122

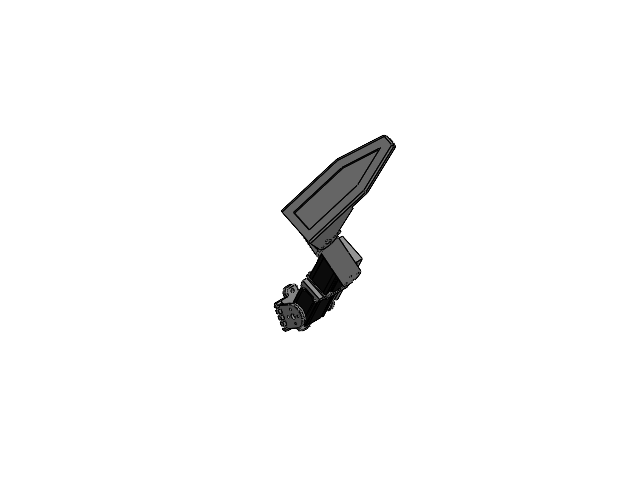
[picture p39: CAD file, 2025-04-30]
CAD SOLIDWORKS/EnsamblePata_Solid.SLDASM
UnionCuerpo.ipt
tibianueva.ipt
femurAux.ipt
Coxa.ipt
tibiaMot.0004.ipt
YB-SD15M-Bottom-Cover-LD v2 x 3
YB-SD15M-Middle-Cover-LD v2 x 3
YB-SD15M-Top-Cover-LD v3 x 3
AuxRudderDisk v2.ipt x 3
RudderDisk v2.ipt x 3

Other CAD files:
CAD SOLIDWORKS/Hexapod.SLDASM
CAD SOLIDWORKS/EnsambleMotor_Solid.SLDASM
hexapod_description/meshes/6B_link.STL
hexapod_description/meshes/6C_link.STL
CAD SOLIDWORKS/hexapod_description/meshes/1A_link.STL
CAD SOLIDWORKS/hexapod_description/meshes/1B_link.STL
CAD SOLIDWORKS/hexapod_description/meshes/1C_link.STL
CAD SOLIDWORKS/hexapod_description/meshes/2A_link.STL
CAD SOLIDWORKS/hexapod_description/meshes/2B_link.STL
CAD SOLIDWORKS/hexapod_description/meshes/2C_link.STL
CAD SOLIDWORKS/hexapod_description/meshes/3A_link.STL
CAD SOLIDWORKS/hexapod_description/meshes/3B_link.STL
CAD SOLIDWORKS/hexapod_description/meshes/3C_link.STL
CAD SOLIDWORKS/hexapod_description/meshes/4A_link.STL
CAD SOLIDWORKS/hexapod_description/meshes/4B_link.STL
CAD SOLIDWORKS/hexapod_description/meshes/4C_link.STL
CAD SOLIDWORKS/hexapod_description/meshes/5A_link.STL
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

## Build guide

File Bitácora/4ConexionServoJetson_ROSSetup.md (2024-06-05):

# Reporte Semana 4
Control de servomotores

## Deberes
- 1)Conexion de servo a la tarjeta Jetson
- 2)Instalación de ROS Noetic en Jetson

-3)Instalacion de máquina virtual con ROS Noetic para continuar con la programación.

  ## 1)Conexion de servo a la tarjeta Jetson
### Conexion puerto serie del driver a la Jetson
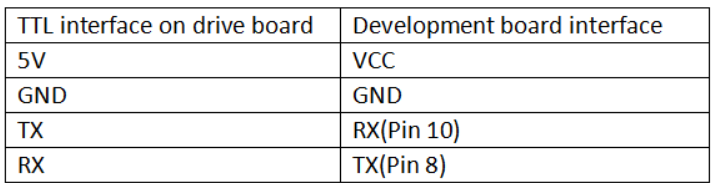
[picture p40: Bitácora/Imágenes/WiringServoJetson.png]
ConexionServoSerial

### Pinout Servo
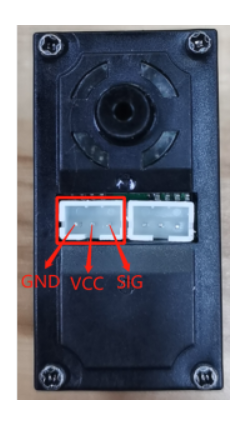
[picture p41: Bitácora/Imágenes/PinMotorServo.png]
PinoutServo


 > Nota: 
 Tuve que instalar  *$ pip3 install pyserial* en la terminal de la jetson y ademas agregar en la primera celda del Jupyternotebook *!pip3 install pyserial*

  ## 3)Instalacion de máquina virtual con ROS Noetic para continuar con la programación.

Se instaló la máquina virtual Semestre 2024-1

A continuación se desarrollará a partir del siguiente repositorio:
> https://github.com/noshluk2/ROS2-Ultimate-guide-for-Custom-Robotic-Arms-and-Panda-7-DOF/tree/master/bazu

Contiene tutoriales para desarrollar un brazo robótico. 

1. Abrir terminal y activar ROS Noetic
   > rosact ros1
3. Entrar a carpeta de desarrollador ROSDev
4. Crear espacio de trabajo
  > $ mkdir -p bazu_ws/src
4. Entrar al espacio de trabajo y compilar
  > $ cd bazu_ws

  > $ catkin_make

5.Entrar a la carpeta src y crear el paquete description y agregar la libreria rospy
  > $ catkin_create_pkg bazu_description rospy

6. Descargar la carpeta de github y copiar los archivos dentro de bazu a nuestra carpeta local de bazu_ws/src
7. Regresar a la carpeta del espacio de trabajo y hacer un catkin
  > $ catkin_make

8. Agregar alias
   >$ cd
   
   >$ gedit .bash_aliases
9. Dentro del bash_aliases añadir la linea y guardar el archivo
   > source ~/ROSDev/bazu_ws/devel/setup.bash
10. Probamos que el paquete funciona, entramos a ROSDev/bazu_ws_devel y ejecutamos
    >$ roslaunch bazu joint_trajectory_controller_bazu.launch

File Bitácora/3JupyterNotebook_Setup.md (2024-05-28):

# Reporte Semana 3
Control de servomotores

## Deberes
- 1)Instalación de Jupyter Notebook
 > **Para realizar caracterización de los servomotores**
- 2)Modificar eslabón union cuerpo y femur para que tenga mas soporte

  ## 1)Instalación de Jupyter Notebook
  - Instalar python requerido y jupyter notebook
  - Crear nuevo jupyter notebook
  - Creacion de carpeta donde trabajar el proyecto "HEXAPODJNB"
  - Creación de subcarpeta "PruebasServo"
  - Agregar el archivo "jetson_bus_servo.ipynb
    >Se encuentra en la sección Control Course 6.2 JetsonNANO http://www.yahboom.net/study/YB-SD15M 

  ## 2)Modificar eslabón union cuerpo y femur para que tenga mas soporte
  
  ### Unión Cuerpo V2
  Se agregaron "costillas" externas y chaflan interior para un mejor soporte de la pieza y evitar concentradores de esfuerzos.
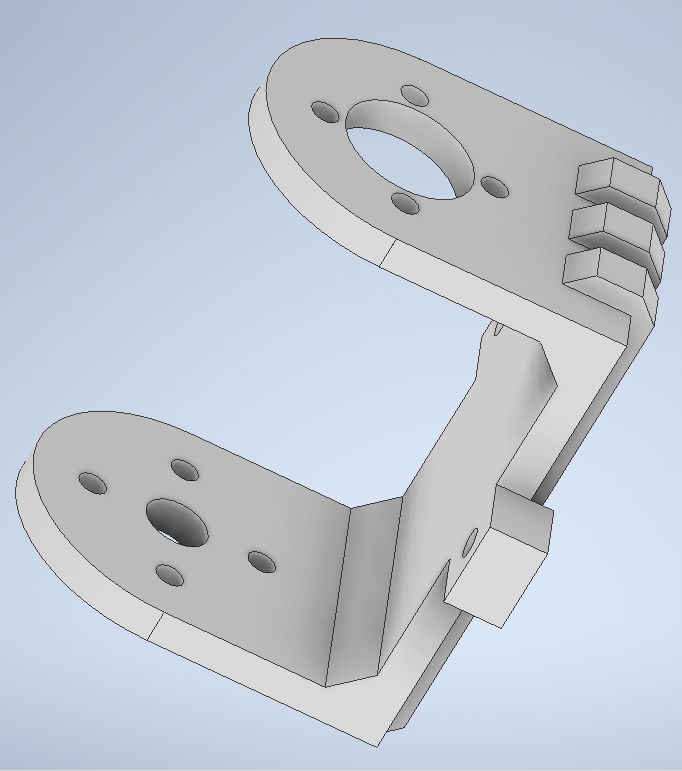
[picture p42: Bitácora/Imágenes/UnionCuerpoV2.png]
UnionCuerpoV2


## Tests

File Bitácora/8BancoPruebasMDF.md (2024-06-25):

# Creación del banco de pruebas para el robot.
Se elaboró un banco de pruebas para poder ensamblar las patas a una base estable y poder probar su funcionamiento y rangos de movimmiento.
El banco puede sostener las 6 patas y se encuentra elevado del "piso" para poder probar las longitudes totales del robot sin colisiones.

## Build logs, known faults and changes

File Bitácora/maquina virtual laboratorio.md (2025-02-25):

Se instalo una maquina virtual completa otorgada por el laboratorio de robotica, para instalar el paquete del scara y tener mejor visualizacion del urdf RLab2025-1_gz

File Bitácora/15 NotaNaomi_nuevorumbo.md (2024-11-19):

# Se tomó un nuevo rumbo

- Hoy intenté conectarme a la driver de los servos pero raspberry pi no la detectaba, así que volveremos a la jetson Nano utilizando un programa del profe felipe, algo como docker y poder usar ros 2 en la JETSON
de este modo ROS 2 controlara solo los motores en la jetson y todos los demas comandos y procesos se ejecutan desde la alien.

- Por otro lado el urdf tenia problemas donde mete todo a un link y no se ven todas las piezas exportadas, entonces creamos en onshape una exportacion de los ensambles a step y luego otra a solidworks, para poder hacer la exportacikon de urdf directamente desde solidworks.

  >cuerpo
  
  >eslabon1
  
  >eslabon2
  
  >eslabon3

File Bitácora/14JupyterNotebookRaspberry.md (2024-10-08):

#Instalacion de Jupyter Notebook

>sudo apt install jupyter-notebook
>jupyter notebook --browser=chromium    o  copiar la url y pegar en navegador

Se descargo el archivo RaspberryPi_bus_servo.py
 en el apartado control course 
 
> http://www.yahboom.net/study/YB-SD15M

Es un código python, por lo que intentare pasarlo a un jpynb para que sea similar al de jetson

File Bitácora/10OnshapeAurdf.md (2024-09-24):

# Conversión de ensamble ONSHAPE A URDF
> https://www.youtube.com/watch?v=TJeCpGnX508&t=195s

Primero instalamos 
> sudo pip install onshape-to-robot

luego agregamos el repositorio
> sudo add-apt-repository ppa:openscad/releases

> sudo apt-get update

> sudo apt-get install openscad -y

> sudo apt-get install meshlab -y

luego obtenemos nuestra API key de Onshape por que onshape to robot la necesita de esta pag web https://dev-portal.onshape.com/keys:

The API key's access key is oHISbRJUvbh6Ia6ao682Nn2z and the secret key is DKSkAOk3KgUVR44pqp5R24mw9GGcATouJtPttQjtDVx7oBNG 
Please transfer this securely to your application now as you will not be able to display this secret key string again.

Ahora crearemos un archivo que almacene esta API KEY para no tener que recordarla y tambien para que se pueda leer a traves de otros programas. Este earchivo estara dentro del workspace, dentro de la carpeta src, el archivo se llamara Keys.txt 
Luego dentro del mismo directorio se crea el archivo "keys.sh"
>touch keys.sh
y se le otorgan permisos
>chmod -x keys.sh

Dentro de este archivo se encuentra:
export ONSHAPE_API=https://cad.onshape.com
export ONSHAPE_ACCESS_KEY=oHISbRJUvbh6Ia6ao682Nn2z
export ONSHAPE_SECRET_KEY=DKSkAOk3KgUVR44pqp5R24mw9GGcATouJtPttQjtDVx7oBNG

> luego se da un source al archivo con $ source keys.sh
> despues $ echo ONSHAPE_ACCES_KEY oHISbRJUvbh6Ia6ao682Nn2z

Regresamos a la carpeta source y creamos un paquete
> ros2 pkg create --build-type ament_cmake hexapod_description --dependencies urdf xacro

Después dentro de hexapodLegC_description crear las siguientes carpetas
> mkdir legC

> mkdir legC/config.json

> mkdir launch

> mkdir rviz
Después configurar en json:
> {
"documentId": "7c09b0c31d867776bda81da9", 
"outputformat" :"urdf",
"packageName": "hexapod_description/hexapodv1",
"robotName": "hexapod",
"assemblyName":"ensambleC"
}

>donde document id viene en la URL de documento y assembly name es el nombre del ensamble en de documento.
Luego editamos CMakeLists.txt y agregamos las nuevas carpetas
install(
  DIRECTORY 
    rviz
    launch
    hexapodv1
  DESTINATION
    share/${PROJECT_NAME}/
)
>antes del ament_package()

>pip install numpy==1.24

>ejecutamos dentro de la carpeta de description $ onshape-to-robot legC

Añadimos la siguiente linea en el archivo robot.urdf
> <?xml version="1.0">

Despues creamos las siguientes carpetas

>touch launch/hexapodv1.launch.py

>touch launch/start_rviz.launch.py

>touch rviz/hexapodv1.rviz

Dentro del archivo hexapodv1.launch.py ingresamos el siguiente codigo:

    import os
    from launch import LaunchDescription
    from launch_ros.actions import Node

    #Función que el sistema de lanzamiento buscará
    def generate_launch_description():

    ####### ENTRADAS DE DATOS #####
    urdf_file = 'robot.urdf'
    package_description = "hexapod_description"

    ###### FIN DE ENTRADAS DE DATOS #####
    print("Fetching URDF ==>")
    
    # Ruta correcta al archivo URDF en la carpeta 'src'
    robot_desc_path = os.path.join(
        '/home/tsmusr/ROS2Dev/hexapod_ws/src',  # Ruta fija a src
        package_description, 'hexapodv1', urdf_file  # Combinación correcta de directorios
    )

    # Verifica si el archivo URDF existe
    if not os.path.exists(robot_desc_path):
        raise FileNotFoundError(f"El archivo URDF no se encuentra en la ruta: {robot_desc_path}")

    # Nodo de Robot State Publisher
    robot_state_publisher_node = Node(
        package="robot_state_publisher",
        executable="robot_state_publisher",
        name="robot_state_publisher_node",
        emulate_tty=True,
        parameters=[{'use_sim_time': True,
                     'robot_description': open(robot_desc_path).read()}],  # Leer directamente el archivo URDF
        output="screen"
    )

    # Crear y devolver el objeto de descripción de lanzamiento
    return LaunchDescription(
        [
            robot_state_publisher_node
        ]
    )

LUEGO en el archivo start_rviz.launch

    import os

    from ament_index_python.packages import get_package_share_directory
    from launch import LaunchDescription
    from launch.substitutions import Command
    from launch_ros.actions import Node

    #this is the function launch system will look for

    def generate_launch_description():
    
    package_description="hexapod_description"

    #RVIZ Configuration
    rviz_config_dir = 
             os.path.join(get_package_share_directory(package_description),'rviz','hexapodv1.rviz')

     rviz_node = Node(
        package='rviz2',
        executable='rviz2',
        output='screen',
        name='rviz_node',
        parameters=[{'use_sim_time':True}],
        arguments=['-d',rviz_config_dir]
    )

    #create and return launch description object
    return LaunchDescription(
        [
            rviz_node
        ]
    )

FINALMENTE Compilamos desde hexapod_ws
>source install/setup.bash

>colcon build --packages-select hexapod_description

>source install/setup.bash

>ros2 launch hexapod_description hexapodv1.launch.py

Se abre otra terminal

>source install/setup.bash

>ros2 launch hexapod_description start_rviz.launch.py

se abre otra terminal

>source install/setup.bash

>ros2 run joint_state_publisher_gui joint_state_publisher_gui

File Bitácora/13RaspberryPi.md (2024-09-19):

# Setup Raspberry Pi 4 ModelB 4GB RAM

 Se siguieron los pasos de Raspberry 
 
distribucion: Debian GNU/Linux 12 (bookworm)

Instalacion Python

> sudo apt update

> sudo apt upgrade

> sudo apt install python3

> python3 --version
la version instalada es Python 3.11.2

Instalacion pip

> sudo apt install python3-pip

> pip3 --version
la veriion instalada es 23.0.1

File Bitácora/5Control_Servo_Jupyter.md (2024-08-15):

# Reporte Semana 5

## Deberes
- 1)Asignación de IDs a los servomotores usando python (JNB)
- 2)Mover 2 servomotores a la vez, realizando diferentes movimientos entre sí. (JNB)

  ## 1)Asignación de IDs a los servomotores usando python (JNB)
  Control de IDs

>  sudo chmod 777 /dev/ttyTHS1  
> jetson_bus_servo-SetID.ipynb

- 1)Duplicar el archivo original de jetson_bus_servo y cambiarle el nombre para realizar las pruebas del cambio de ID.
- 2)Dentro del nuevo archivo se asigna el index que se quiere para el motor, se corre todo el proceso, se desconecta el motor y se repite para el siguiente motor cambiandole el id.

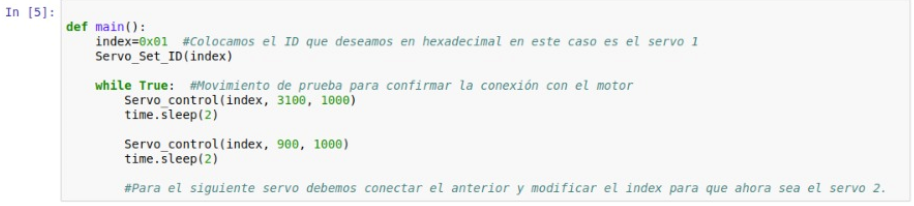
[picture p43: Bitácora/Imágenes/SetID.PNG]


  ## 2)Mover 2 servomotores a la vez, realizando diferentes movimientos entre sí. (JNB)
  Control de múltiples servomotores
> jetson_bus_servo-CONTROL.ipynb
- 1)Ejecutar todas las celdas del archivo, podremos controlar los diferentes servomotores indicando su ID colocando su index en hexadecimal respectivamente.

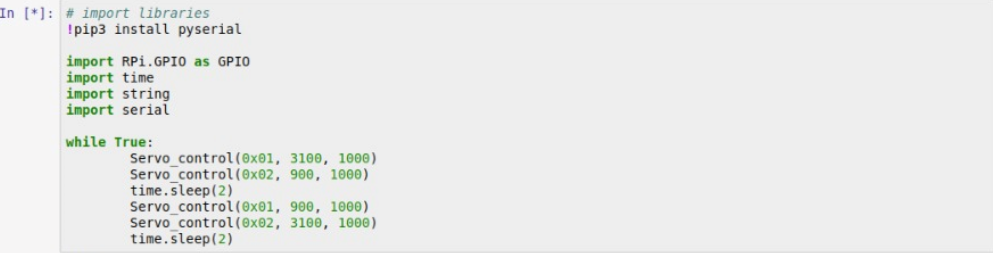
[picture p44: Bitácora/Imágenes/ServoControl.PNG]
Set Servo ID


## Orden de los IDs en los motores del hexápodo:
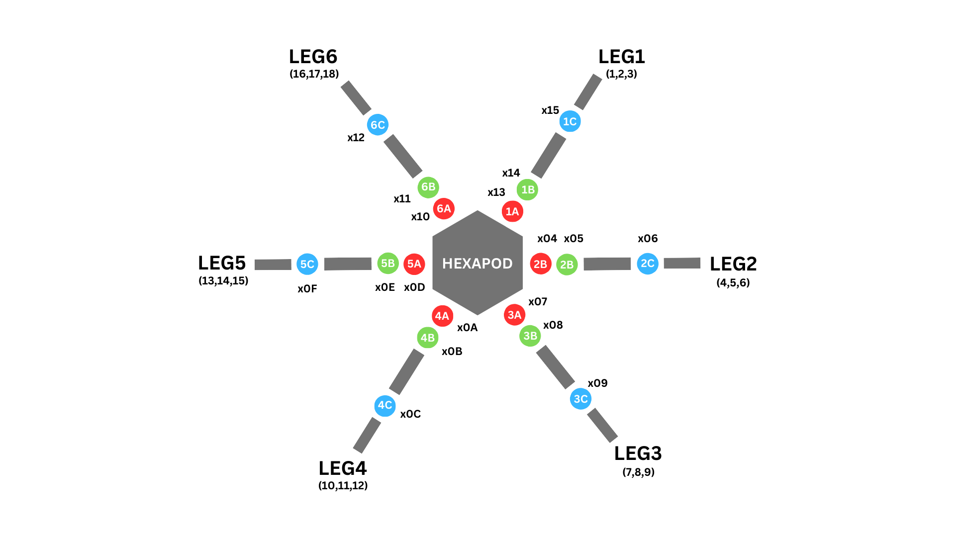
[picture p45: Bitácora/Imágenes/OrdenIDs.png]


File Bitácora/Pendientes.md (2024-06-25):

# PENDIENTES

- Asignar ID a motores.
- Realizar esquema de la organización de las patas.
- Establecer los motores en su cero.
- Banco de pruebas MDF.
- Ensamble CAD pata.  DXF
- Controlador de la pata.
- Onshape download para exportar URDF.

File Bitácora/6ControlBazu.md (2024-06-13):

# Reporte Semana 6
Todo esto se realizó en la máquina virtual 
> TSR2024-1

## Deberes
- 1)Integrar los paquetes que hacen falta para poder mover el modelo en RVIZ 
- 2)Mover el modelo en RVIZ

  ## 1)Integrar los paquetes que hacen falta para poder mover el modelo en RVIZ 
En el reporte 4 se realizó la instalación de la carpeta bazu, sin embargo al ejecutar el topico en ROS y RVIZ marca varios errores, por lo que hace falta integrarle otros archivos, estos archivos sirven para tener de manera independiente el effort controller y el position controller.
  De manera que la distribución de archivos dentro de las carpetas queda de la siguiente manera:
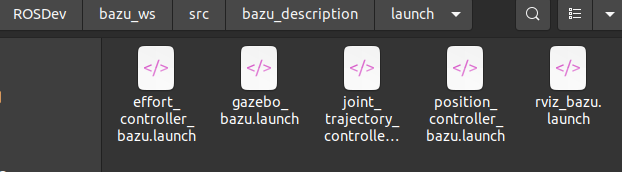
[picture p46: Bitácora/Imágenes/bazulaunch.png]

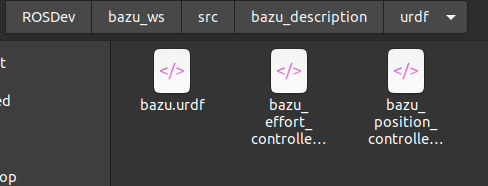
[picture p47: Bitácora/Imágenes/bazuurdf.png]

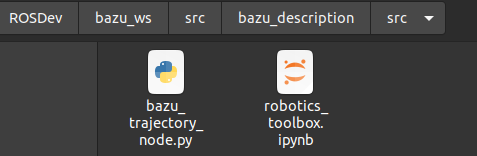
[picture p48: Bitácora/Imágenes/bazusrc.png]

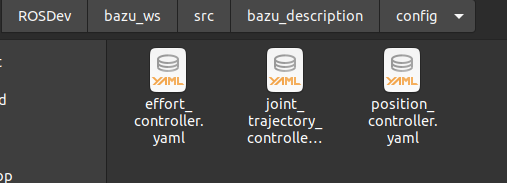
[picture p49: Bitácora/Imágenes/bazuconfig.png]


Ahora para compilar debemos ejecutar
> $ catkin_make
Y refrescar la fuente
> $ source devel/setup.bash

  ## 2)Mover el modelo en RVIZ
Debemos enviar el mensaje a través del publicador (por consola con ROS), entonces debemos publicar en dos lados, en rviz y en python para que se simule y se muevan los motores en tiempo real. 

> $ roslaunch bazu position_controller_bazu.launch
Abrir otra terminal para leer los topicos
> $ rostopic list

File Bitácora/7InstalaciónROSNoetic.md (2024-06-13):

# Instalación de ROS NOETIC EN LA JETSON NANO 
> Siguiendo las instrucciones en la siguiente página: https://gist.github.com/Pyrestone/ef683aec160825eee5c252f22218ddb2

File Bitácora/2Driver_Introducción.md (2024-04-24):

# Reporte Semana 2
Introducción al driver para los servomotores

## Deberes
- 1)Caracterización de los servomotores (ángulos)
 > **Pendiente**
- 2)Investigación puertos UART RX,TX
- 3)Investigación librería python smbus2
- 4)Prueba de ensamble eslabones

##  1) Caracterización de los servomotores (ángulos)
> **Completado** 

## 2) Investigación puertos UART RX,TX
Un UART es un tipo de circuito integrado que se usa para enviar y recibir datos a través de un puerto serie en un equipo o dispositivo periférico. Los UART son ampliamente utilizados y conocidos por su sencillez. Sin embargo, a diferencia de SPI e I2C, los UART no admiten múltiples dispositivos subordinados.

Un puerto UART (Universal Asynchronous Receiver/Transmitter) es un componente de hardware que permite la comunicación serial entre dispositivos. "RX" significa "Receptor" y "TX" significa "Transmisor".

RX (Receptor): Es el pin de entrada en el que un dispositivo recibe datos de otro dispositivo.
TX (Transmisor): Es el pin de salida en el que un dispositivo envía datos a otro dispositivo.
Por lo tanto, cuando se conectan dos dispositivos a través de un puerto UART, el pin TX de un dispositivo se conecta al pin RX del otro dispositivo, y viceversa. Esta conexión permite la comunicación bidireccional de datos entre los dispositivos. Es común encontrar puertos UART en microcontroladores, módulos de comunicación inalámbrica, dispositivos de IoT, entre otros.

El UART opera de manera asíncrona, lo que significa que no requiere un reloj de sincronización entre el transmisor y el receptor. En lugar de eso, los dispositivos acuerdan de antemano una velocidad de transmisión (baud rate) para la comunicación, lo que determina la duración de cada bit y el intervalo entre bits. Esto permite la comunicación serial entre dispositivos que pueden estar utilizando diferentes relojes o velocidades de procesamiento.

## 3) Investigación librería python smbus2
Comunicación con sensores y dispositivos periféricos: Muchos sensores y dispositivos periféricos utilizan el protocolo SMBus para la comunicación con la CPU u otros componentes de un sistema electrónico. La librería SMBus proporciona una forma de interactuar con estos dispositivos desde el software del sistema.
Monitoreo del sistema: El protocolo SMBus también se utiliza para acceder a información de monitoreo del sistema, como la temperatura, el voltaje y la velocidad del ventilador de la CPU. La librería SMBus permite a los programas acceder a estos datos y realizar acciones basadas en ellos, como ajustar la velocidad del ventilador para mantener la temperatura dentro de límites seguros.
Configuración del sistema: Algunos dispositivos pueden ser configurados a través del protocolo SMBus. Por ejemplo, se pueden ajustar parámetros de funcionamiento o activar características específicas de un dispositivo mediante comandos enviados a través del bus SMBus.

> FUENTE: https://pypi.org/project/smbus2/
> https://www.youtube.com/watch?v=G7aQB6x0LHc

## 4) Prueba de ensamble eslabones

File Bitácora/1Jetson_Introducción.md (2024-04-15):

# Reporte Semana 1
Introducción a la tarjeta Jetson Nano 

## Deberes
- 1)Añadir imagen a la tarjeta siguiendo en tutorial de la página:
  https://developer.nvidia.com/embedded/learn/getting-started-jetson

- 2)Documentación Pinout de la tarjeta Jetson
- 3)Documentación de la tarjeta driver para los servomotores

##  1) Añadir imagen a la tarjeta 
> **Completado** 

## 2) Documentación Pinout de la tarjeta Jetson
### Esquemático de la tarjeta (Top y Bottom View)

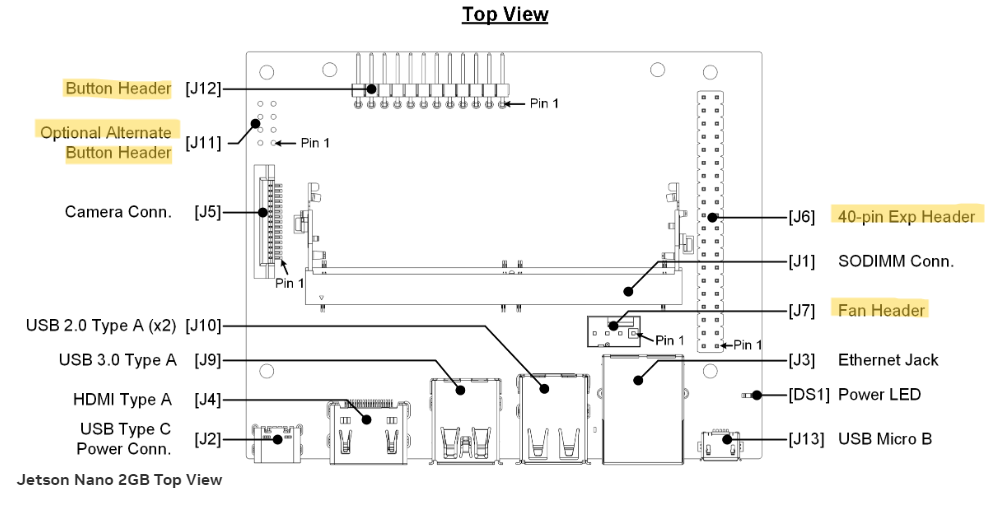
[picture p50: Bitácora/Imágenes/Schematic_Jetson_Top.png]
Jetson_Top

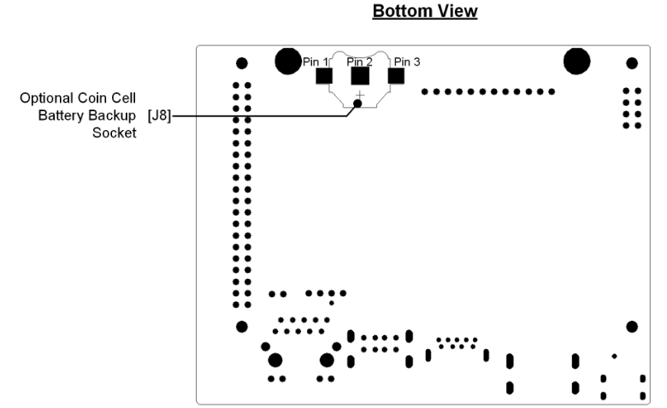
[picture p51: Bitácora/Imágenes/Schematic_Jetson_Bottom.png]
Jetson_Bottom


### Pinout de [J6] 40-pin Exp Header
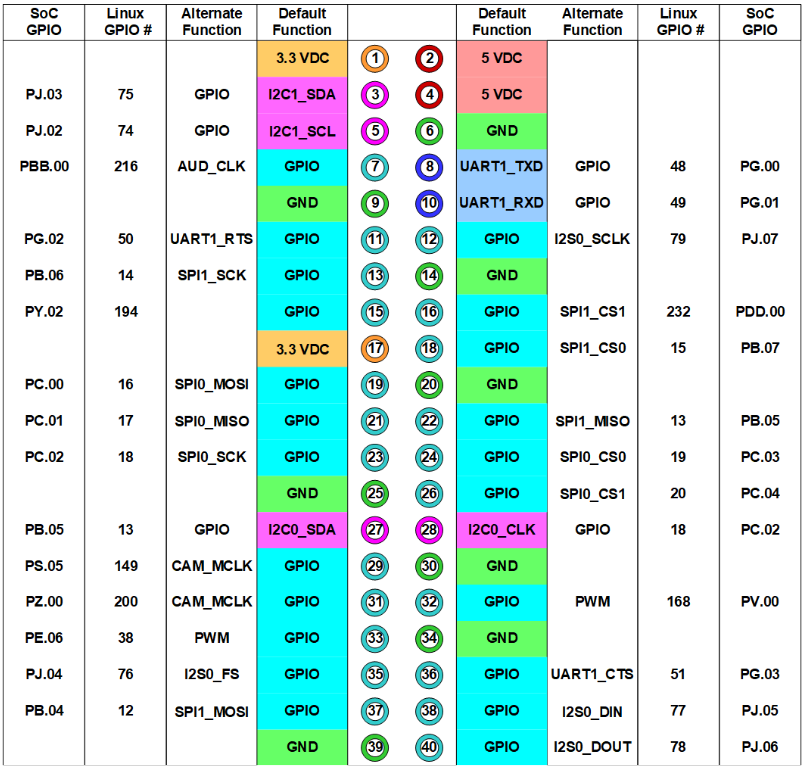
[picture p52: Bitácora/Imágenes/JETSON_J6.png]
Jetson_J6

### Pinout de [J7] Fan Header
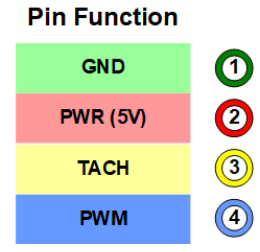
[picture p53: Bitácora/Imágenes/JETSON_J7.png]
Jetson_J7

### Pinout de [J11] Optional Alternate Button Header
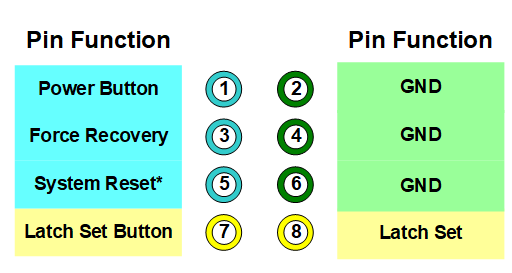
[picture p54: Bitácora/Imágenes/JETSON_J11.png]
Jetson_J11

### Pinout de [J12] Button Header
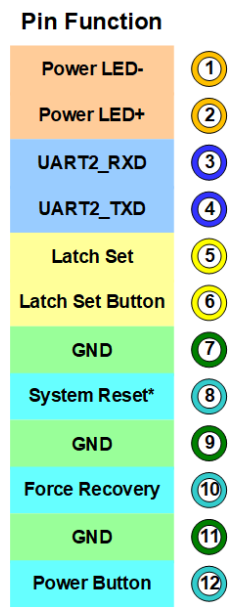
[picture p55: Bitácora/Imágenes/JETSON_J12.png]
Jetson_J5


>  FUENTE: https://developer.nvidia.com/embedded/learn/jetson-nano-2gb-devkit-user-guide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

## 3) Documentación de la tarjeta driver para los servomotores
### Esquemático del driver
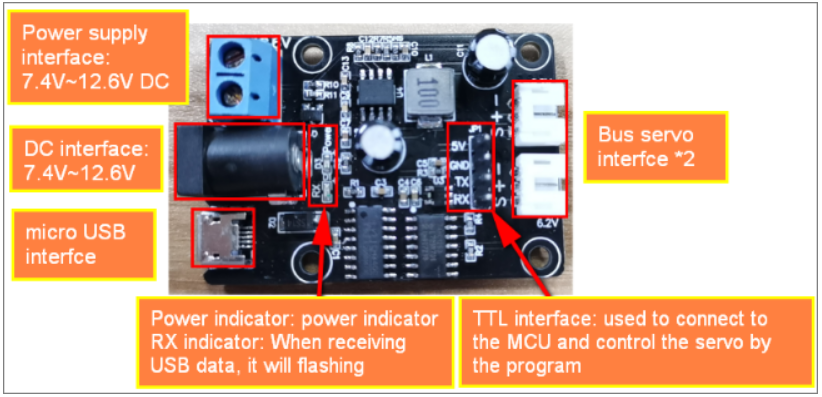
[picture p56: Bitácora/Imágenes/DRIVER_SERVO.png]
DRIVER_SERVO

### Instalación del driver CH340
Es necesario para detectar el puerto COM

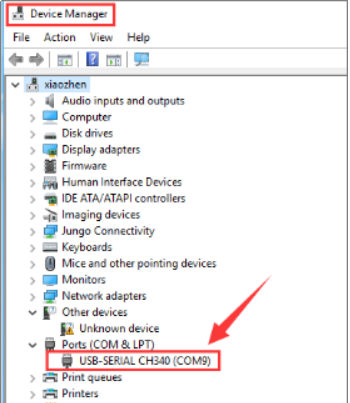
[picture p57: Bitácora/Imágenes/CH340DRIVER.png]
CH340

### Inicializar motores
 Double-click to open the servo debugging software. Click [Settings]-- [Serial Port Settings] to select the corresponding port number, the baud rate is 115200, and finally click [Open Port].

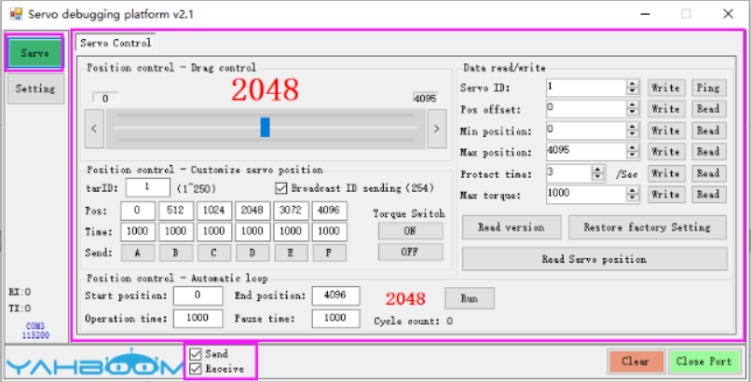
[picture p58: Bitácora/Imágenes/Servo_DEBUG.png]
SERVODEBUG


>  FUENTE: http://www.yahboom.net/study/YB-SD15M

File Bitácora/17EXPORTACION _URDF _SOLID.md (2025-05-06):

Se siguió el tutorial para la exportacion como en el video a excepcion de la modificacion de los archivos CMakeLists.txt  y package.xml en la carpeta de hexpapode description (tambion se creo el workspace para el hexapodo), estos archivos se tomaron del robot scara y se modificaron para el hexapodo, así ya funcionan para ROS2.

En solidworks se realizo el ensmble y se ajustaron las posiciones de inicio del hexapodo con relaciones de posicion con paralelas y angulos

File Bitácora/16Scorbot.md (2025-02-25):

# REVISIÓN DEL CONTROLADOR SCORBOT QUE ES SIMILAR

1. Descargar archivo
2. Extraer en ROS2DEV
3. revisar en terminal
4. acceder a la carpeta
5.  hacer rm build install y log por que ya estaba compilado previamente con otra computadora y las rutas del cmake interfieren, entonces las borramos.
6.  hacer ~colcon build para crear estas carpeta denuevo y compilar dentro de nuestra ruta.
   
7.hacer carpeta world dentro de bringup description ya que marcaba error por que se habia borrado en la importacion por estar vacía
8. ~source install/setup.bash
   
10. ~ros2 launch scorbot_bringup trajectory_controller_scorbot.launch.py esto abre gazebo y rviz

11. ~ros2 launch scorbot_description scorbot_display.launch.xml abre RVIZ con el controlador de posición

> nota:el paquete del scorbot tiene un jupyter notebook llamado reporte examen, que explica mejor todo.

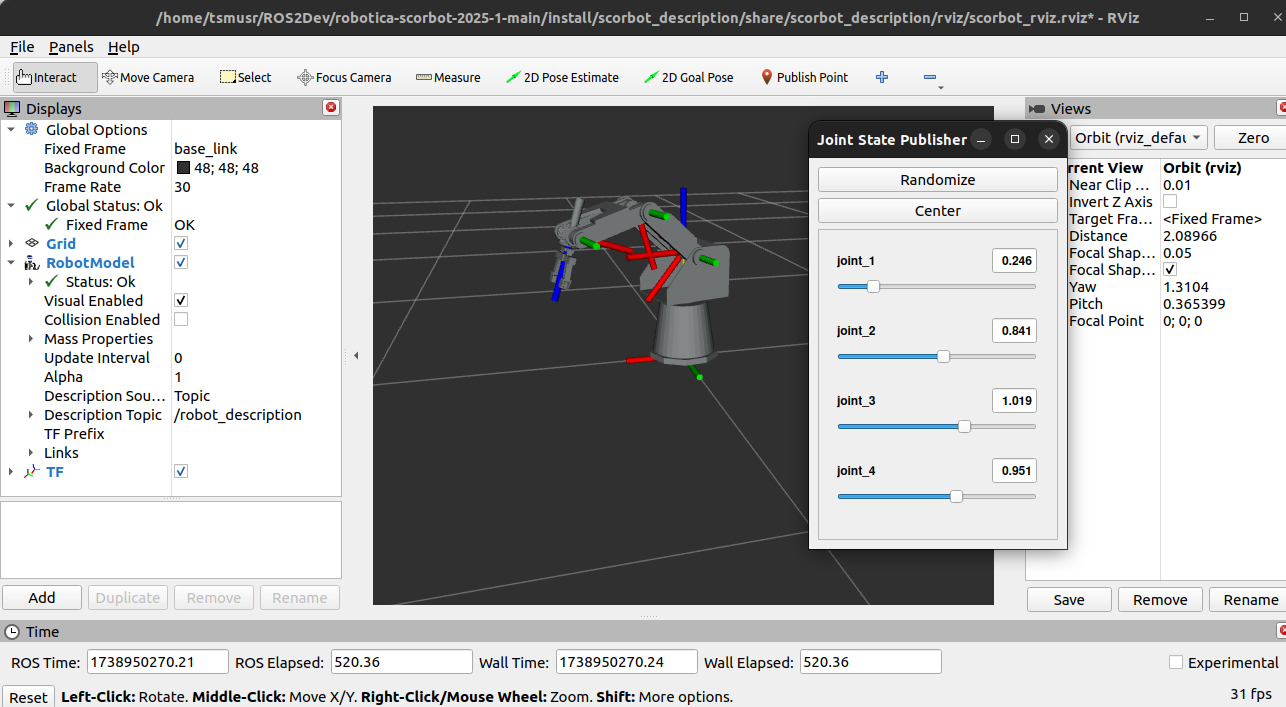
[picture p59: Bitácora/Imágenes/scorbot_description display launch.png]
Scorbot_launch
 

SE HIZO CON EL CONTROLADOR DEL DOFBOT DEL PROFE ERIK

asegurarse de meter los paquetes dentro de una carpeta src, se hizo la instalacion requerida para los controladores segun el ipynb conceptos basicos dentro del paquete en la parte, "configuracion básica de una junta" 

ROBOT SCARA examen description

~ros2 launch examen_bringup roberto_pos_controller_scara.launch.py
hacer ~source install/setup.bash
~ros2 run examen_bringup multi_tray.py

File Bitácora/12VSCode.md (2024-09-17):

#Instalación de VS CODE

Visual studio no esta configurado para esta distribución de Ubuntu en Jetson Nano por lo que se deecidio 
usar una conexión Remota desde otro equipo por SSH.

El procedimiento fue 

1. Abrir visual studio code desde otro equipo
2. Instalar la extensión SSH Remote
3. Agregar la nueva conexión SSH como hexapod@192.168.50.197 en Linux
 > para obtener la IP se uso $ hostname -I en la terminal de mi hexapodo
5. Abrir un folder, para verificar que estamos enlazados.

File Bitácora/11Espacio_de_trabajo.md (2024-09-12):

# Creación de nuestro workspace

creación de la carepte de desarrollo ROSNoetic_dev
> mkdir ROSNoetic_dev

creacion del workspace del hexapodo

> cd ROSNoetic_dev

> mkdir hexapod_ws

creacion de la carpeta src dentro del workspace

> cd hexapod_ws

> mkdir src

realizar un colcoin build en el workspace (desde hexapod_ws)
> cd ..

> colcon build

NOTA:en caso de no tener colcon instalado ejecutar desde la carpeta raiz de todo
> cd

> pip3 install colcon-common-extensions

> podemos asegurarnos que se instalo con $colcon --help

Una vez que se ejecuta el colcon en la carpeta del espacio de trabajo surgen las carpetas: build, install, log, src

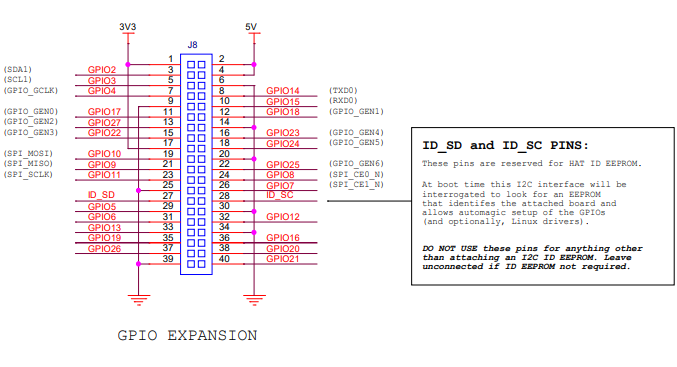
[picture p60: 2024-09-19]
Bitácora/Imágenes/GPIO_Raspberry.png

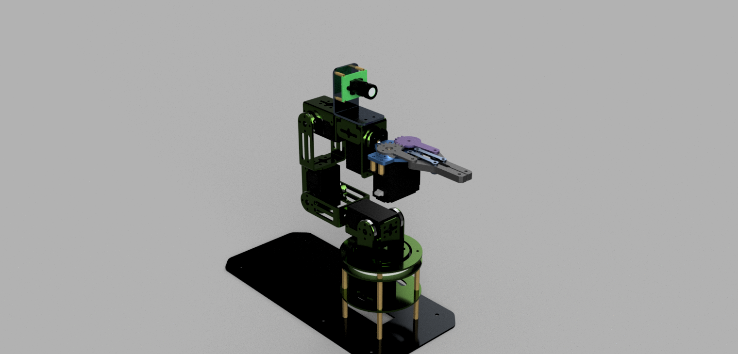
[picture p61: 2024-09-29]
Bitácora/Imágenes/DofbotArm2.png

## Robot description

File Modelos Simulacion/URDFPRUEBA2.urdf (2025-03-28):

<?xml version="1.0"?> 
 <robot name="robot"> 

<!------------------------------------------------------------BASE LINK-->
     <link name="base_link"> 
        <visual>
        <origin xyz="0.0 0.0 0.0" rpy="0 0 0" />
        <geometry>
            <cylinder radius="0.12" length="0.063"/>
        </geometry>
        <material name="grey">
            <color rgba="0.1 0.1 0.1 1.0" />
        </material>
        </visual>
        <collision>
            <origin xyz="0.0 0.0 0.0" rpy="0 0 0" />
            <geometry>
                <cylinder radius="0.12" length="0.063"/>
            </geometry> 
        </collision>
         <inertial>
            <origin xyz="0 0 0" rpy="0 0 0"/>
            <mass value="1"/>
            <inertia ixx="1.0" ixy="0.0" ixz="0.0" iyy="1.0" iyz="0.0" izz="1.0"/>
        </inertial>
     </link> 
<!---------------------------------------------------------------LINK 1-->
    <link name="link_1">
        <visual>
            <origin xyz="0.04 0 0" rpy="0 0 0" />
            <geometry>
                <box size="0.083 0.03 0.04" />
            </geometry>
            <material name="red">
                <color rgba="1 0.0 0.0 1.0"/>
            </material>
        </visual>
        <collision>
            <origin xyz="0.04 0 0" rpy="0 0 0" />
            <geometry>
                <box size="0.083 0.03 0.04" />
            </geometry>
        </collision>

     <inertial>
        <origin xyz="0 0 0" rpy="0 0 0"/>
        <mass value="1"/>
        <inertia ixx="1.0" ixy="0.0" ixz="0.0" iyy="1.0" iyz="0.0" izz="1.0"/>
    </inertial>
    </link>
     
    <joint name="link_1_joint" type="revolute">
        <parent link="base_link"/>
        <child link="link_1"/>
        <axis xyz="0 0 1"/>
        <limit lower="-3.14159" upper="3.14159" velocity="50.0" effort="1000.0"/>
        <origin xyz="0.12 0 0" rpy="0 0 0"/>
        
    </joint>

<!----------------------------------------------------------------- LINK 2-->
     <link name="link_2">
        <visual>
            <origin xyz="0.0975 0 0" rpy="0 0 0" />
            <geometry>
                <box size="0.195 0.03 0.04" />
            </geometry>
            <material name="green">
                <color rgba="0.0 1.0 0.0 1.0" />
            </material>
        </visual>
              <inertial>
        <collision>
            <origin xyz="0.0975 0 0" rpy="0 0 0" />
            <geometry>
                <box size="0.195 0.03 0.04" />
            </geometry>
        </collision>
        <origin xyz="0 0 0" rpy="0 0 0"/>
        <mass value="1"/>
        <inertia ixx="1.0" ixy="0.0" ixz="0.0" iyy="1.0" iyz="0.0" izz="1.0"/>
        </inertial>
         
    </link>


    <joint name="link_2_joint" type="revolute">
        <parent link="link_1"/>
        <child link="link_2"/>
        <axis xyz="0 1 0"/>
        <limit lower="-3.14159" upper="3.14159" velocity="50.0" effort="1000.0"/>
        <origin xyz="0.083 0 0" rpy="0 0 0"/>
    </joint>

<!---------------------------------------------------------------- LINK 3-->
     <link name="link_3">
        <visual>
            <origin xyz="0.061 0.0 0.0" rpy="0 0 0" />
            <geometry>
                <box size="0.122 0.03 0.04" />
            </geometry>
            <material name="blue">
              <color rgba="0.0 0.0 1.0 1.0" />
            </material>
        </visual>
        <collision>
            <origin xyz="0.061 0.0 0.0" rpy="0 0 0" />
            <geometry>
                <box size="0.122 0.03 0.04" />
            </geometry>
        </collision>
              <inertial>
        <origin xyz="0 0 0" rpy="0 0 0"/>
        <mass value="1"/>
        <inertia ixx="1.0" ixy="0.0" ixz="0.0" iyy="1.0" iyz="0.0" izz="1.0"/>
        </inertial>
    </link>

     
    <joint name="link_3_joint" type="revolute">
        <parent link="link_2"/>
        <child link="link_3"/>
        <axis xyz="0 1 0"/>
        <limit lower="-3.14159" upper="3.14159" velocity="50.0" effort="1000.0"/>
        <origin xyz="0.195 0 0" rpy="0 0 0"/>
    </joint>

     
 </robot>

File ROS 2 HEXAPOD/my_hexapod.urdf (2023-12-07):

<?xml version="1.0" ?>
<robot name="my_hexapod" >

    <!-- Propiedades -->

    <material name="color_base">
        <color rgba="0 0 0.5 1" />
    </material>

    <material name="color_red">
        <color rgba="0.5 0 0 1" />
    </material>

    <material name="color_green">
        <color rgba="0 0.5 0 1" />
    </material>

    <!-- Eslabon Vacío (Para que se mueva)-->
    <link name="base_footprint" />

    <!-- Eslabon Base -->
    <link name="base_link">
        <visual>
            <geometry>
                <box size="0.3 0.2 0.10" />
            </geometry>
            <origin xyz="0.0 0.0 0.0" rpy="0 0 0"/>
            <material name="color_base" />
        </visual>
    </link>

    <!-- Juntas para el movimiento -->

    <!-- Junta entre cuerpo vacío y cuerpo base-->
    <joint name="base_footprint_to_base_link_joint" type="fixed" >
        <parent link="base_footprint" />
        <child link="base_link" />
        <origin xyz="0 0 0.15" rpy="0 0 0" />
    </joint>

    <!-- Eslabones Normales -->
    
    <!-- Eslabón COXA -->
    <link name="coxa_p1_link">
        <visual>
            <geometry>
                <box size="0.05 0.15 0.05" />
            </geometry>
            <origin xyz="0.0 0.075 0" rpy="0 0 0"/>
            <material name="color_red" />
        </visual>
    </link>

    <!-- Eslabón FEMUR-->
    <link name="femur_p1_link">
        <visual>
            <geometry>
                <box size="0.05 0.15 0.05" />
            </geometry>
            <origin xyz="0.0 0.075 0.0" rpy="0 0 0"/>
            <material name="color_green" />
        </visual>
    </link>

    <!-- Eslabón TIBIA -->
    <link name="tibia_p1_link">
        <visual>
            <geometry>
                <box size="0.05 0.15 0.05" />
            </geometry>
            <origin xyz="0.0 0.075 0.0" rpy="0 0 0"/>
            <material name="color_base" />
        </visual>
    </link>

    <!-- Juntas para formar la pata-->

    <!-- Junta entre el cuerpo base y el coxa -->
    <joint name="base_link_to_coxa_p1_link_joint" type="revolute">
        <parent link="base_link" />
        <child link="coxa_p1_link" />
        <origin xyz="0.0 0.1 0.005" rpy="0 0 0" />
        <axis xyz="0 0 1" />
        <limit lower="-1.57" upper="1.57" effort="0.176" velocity="0.166" />
    </joint>

    <!-- Junta entre el coxa y el femur -->
    <joint name="coxa_p1_link_to_femur_p1_link_joint" type="revolute">
        <parent link="coxa_p1_link" />
        <child link="femur_p1_link" />
        <origin xyz="0.0 0.15 0.0" rpy="0 0 0" />
        <axis xyz="1 0 0" />
        <limit lower="-1.57" upper="1.57" effort="0.176" velocity="0.166" />
    </joint>

    <!-- Junta entre el femur y la tibia -->
    <joint name="femur_p1_link_to_tibia_p1_link_joint" type="revolute">
        <parent link="femur_p1_link" />
        <child link="tibia_p1_link" />
        <origin xyz="0.0 0.15 0.0" rpy="0 0 0" />
        <axis xyz="1 0 0" />
        <limit lower="-1.57" upper="1.57" effort="0.176" velocity="0.166" />
    </joint>

</robot>

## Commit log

2023-10-25 Create README.md
    Creación de carpeta
2023-11-22 SRC My_hexapod
    [CuerpoHexapod.stl, my_hexapod.urdf]
2023-12-01 Update README.md
    Avances logrados hasta el primero de diciembre 1 del 2023
2023-12-01 Caperta Description
    Carpeta de inicio para la construcción del modelo virtual del robot.
    [hexapod.urdf]
2024-04-11 Jetson PiNOUT
2025-03-26 Create URDFPRUEBA2.urdf
    URDF Con las posiciones definidas en visual,,,, se debe poner al reves, las ubicaciones en joint y visual en origen
    [URDFPRUEBA2.urdf]
2025-03-26 Update URDFPRUEBA2.urdf
    Corregido y funcional en los ejes
    [URDFPRUEBA2.urdf]
2025-03-28 Update URDFPRUEBA2.urdf
    Agrega inertia y collision
    [URDFPRUEBA2.urdf]
2025-05-05 Create EXPORTACION URDF SOLID.md
2025-05-05 Rename EXPORTACION URDF SOLID.md to 17EXPORTACION _URDF _SOLID.md
2025-05-06 versión posicionada
    [1A_link.STL, 1B_link.STL, 1C_link.STL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]
2025-05-08 Nuevo ejeA hexapod_description.urdf
    [hexapod_description.urdf]
2025-06-11 ACTUALIZADO SOLIDWORKS CON EJES DE COORDENADAS CORRECTO en todos los motores
    [1A_link.STL, 1B_link.STL, 1C_link.STL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]
